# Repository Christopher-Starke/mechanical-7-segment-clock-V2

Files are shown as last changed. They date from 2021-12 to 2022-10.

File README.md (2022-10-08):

# mechanical-7-segment-clock-V2
A large mechanical 7-segment clock using cheap stepper motors. This thing is really big about 135x65cm! 

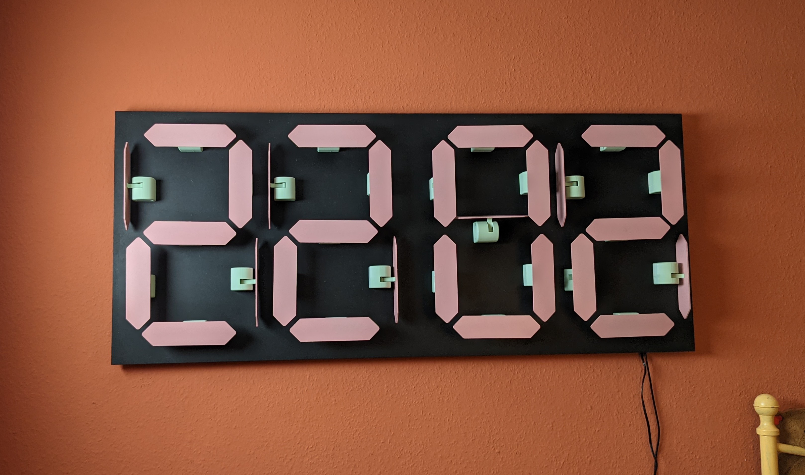
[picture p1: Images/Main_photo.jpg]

##

## BOM
- 28x		28BYJ-48 5V stepper motors (12v steppers also usable with appropriate power supply) 
- 1x		Main controller PCB
- 4x		Stepper breakout PCB
- 1x		button breakout PCB
- 28x		608 skateboard bearings
- 56x		M4x10 bolts (for anchoring stepper motors to the housing)
- 56x 		M4x25 bolts (for attaching the stepper casing to the backboard)
- 4x 		40 Pin ribbon cable connectors
- 1x		6 Pin ribbon cable connector 

### Printed parts 
- 28x 		Stepper housing-Case
- 28x		Stepper housing-Clip
- 28x		Stepper housing-Lever

- 1x		Button breakout - Base
- 1x		Button breakout - Lid

- 4x		Stepper breakout - base
- 4x 		Stepper breakout - lid 

- 1x		Controller - base
- 1x		Controller - lid 

### Cut parts
- 1x 		Backplate 	(18mm MDF)
- 28x		Segment 	(3mm MDF)

meep

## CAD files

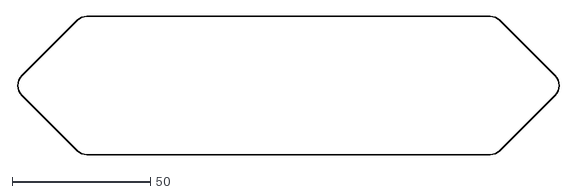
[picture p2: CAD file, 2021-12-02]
hardware/Cut files/Segment.dxf
196.8 x 50.0

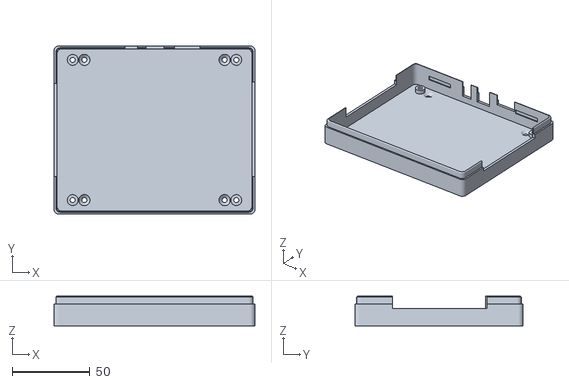
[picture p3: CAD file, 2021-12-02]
hardware/Print files/Electronics cases/Controller - base.stl
129.0 x 108.0 x 19.0

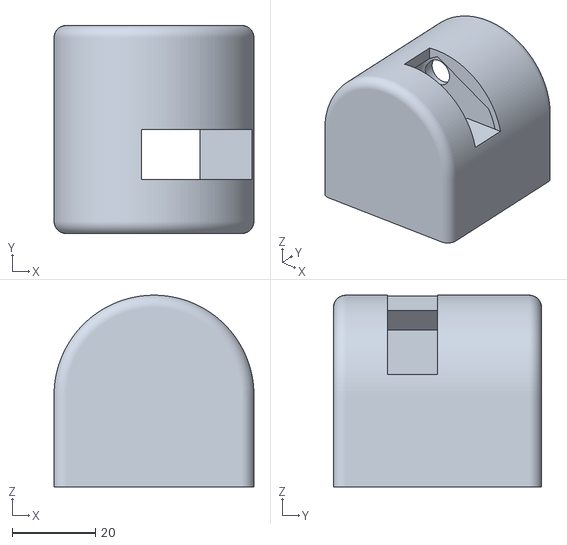
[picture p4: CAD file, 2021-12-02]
hardware/Print files/Stepper housing/Stepper housing - Case.stl
48.0 x 50.0 x 46.0

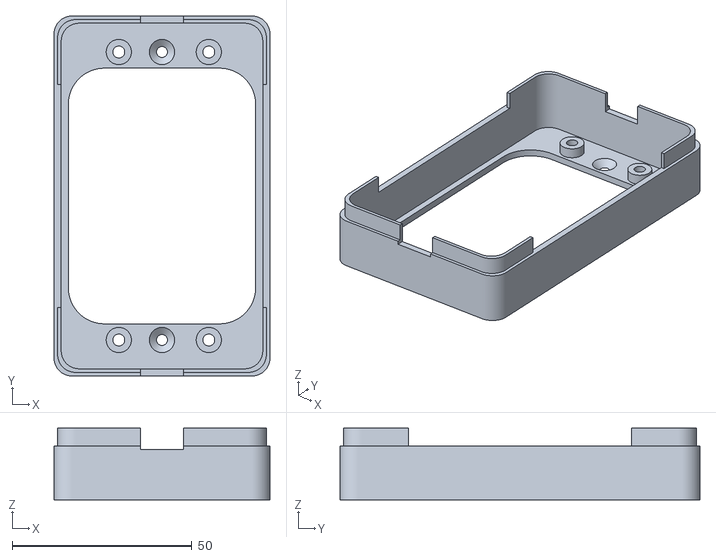
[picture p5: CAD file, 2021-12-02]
hardware/Print files/Electronics cases/Stepper breakout - base.stl
60.0 x 100.0 x 20.0

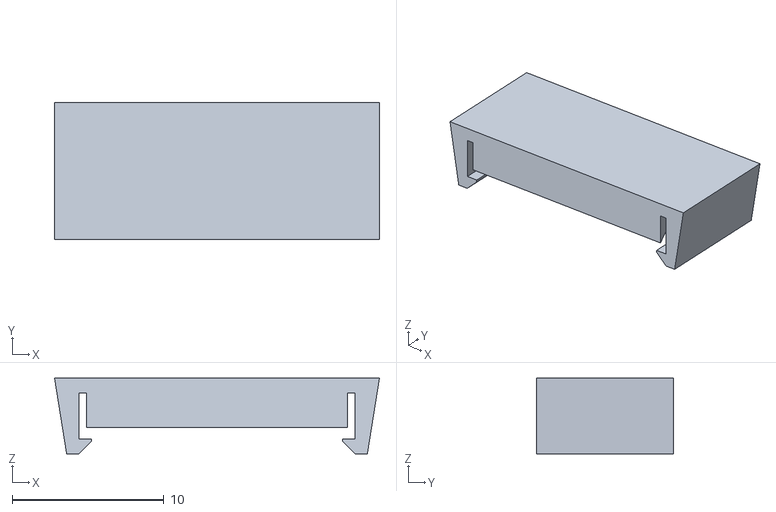
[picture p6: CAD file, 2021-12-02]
hardware/Print files/Stepper housing/Stepper housing - Clip.stl
21.4 x 9.00 x 5.00

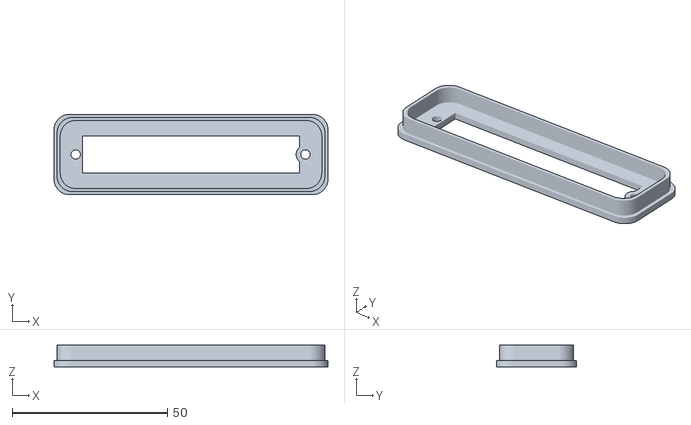
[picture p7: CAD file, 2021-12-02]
hardware/Print files/Electronics cases/Button breakout - Base.stl
88.3 x 25.9 x 7.00

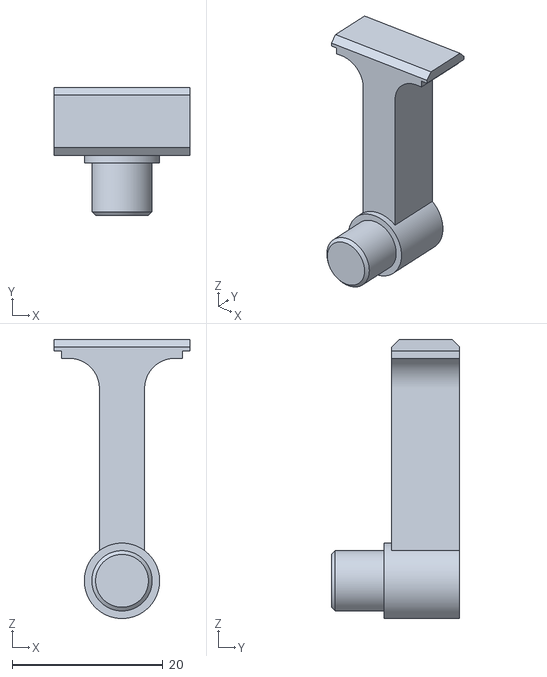
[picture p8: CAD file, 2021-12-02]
hardware/Print files/Stepper housing/Stepper housing - Lever.stl
18.0 x 17.0 x 37.0

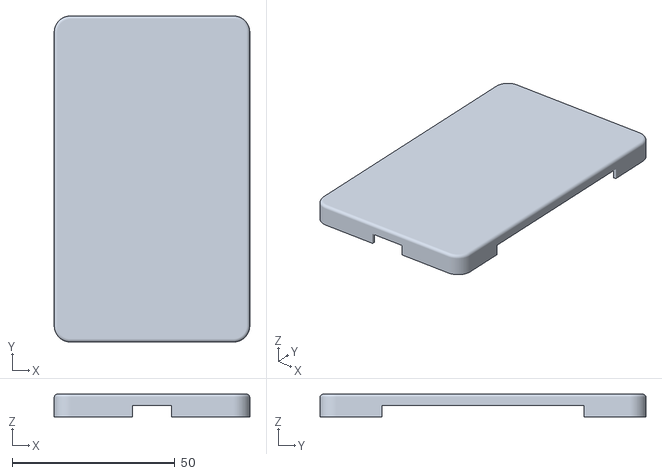
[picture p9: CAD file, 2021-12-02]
hardware/Print files/Electronics cases/Stepper breakout - lid.stl
60.0 x 100.0 x 7.00

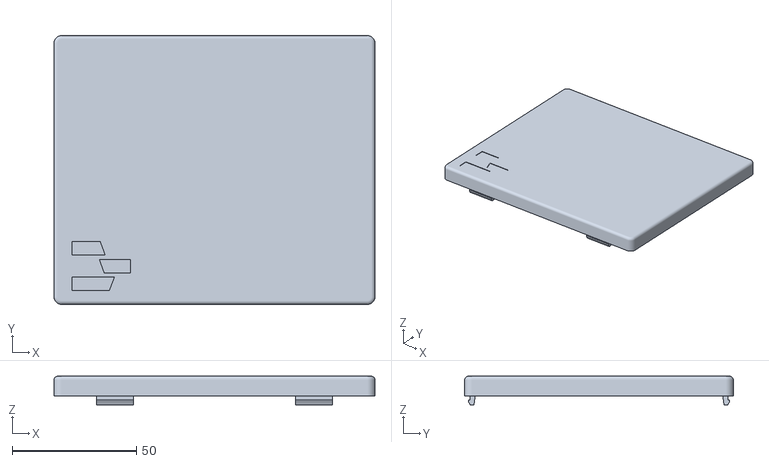
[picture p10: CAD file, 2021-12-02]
hardware/Print files/Electronics cases/Controller - lid.stl
129.0 x 108.0 x 11.5

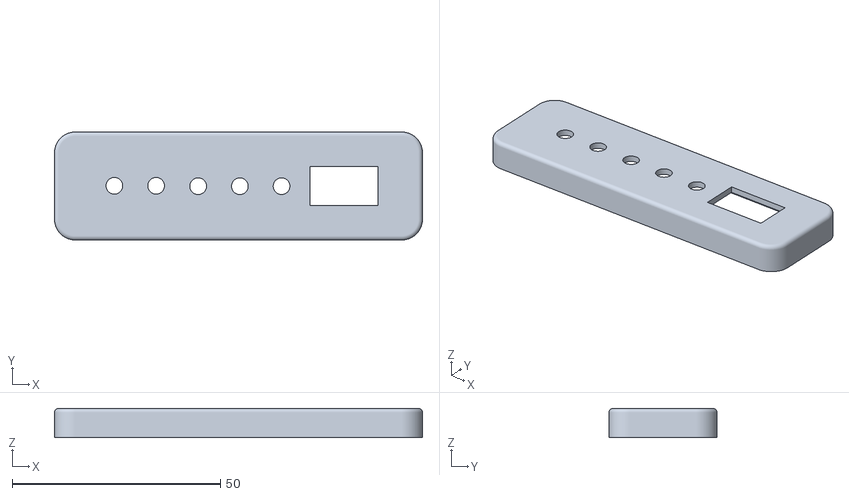
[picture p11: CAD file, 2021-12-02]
hardware/Print files/Electronics cases/Button breakout - Lid.stl
88.3 x 25.9 x 7.00

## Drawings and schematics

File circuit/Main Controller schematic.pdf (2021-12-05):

CN5 1

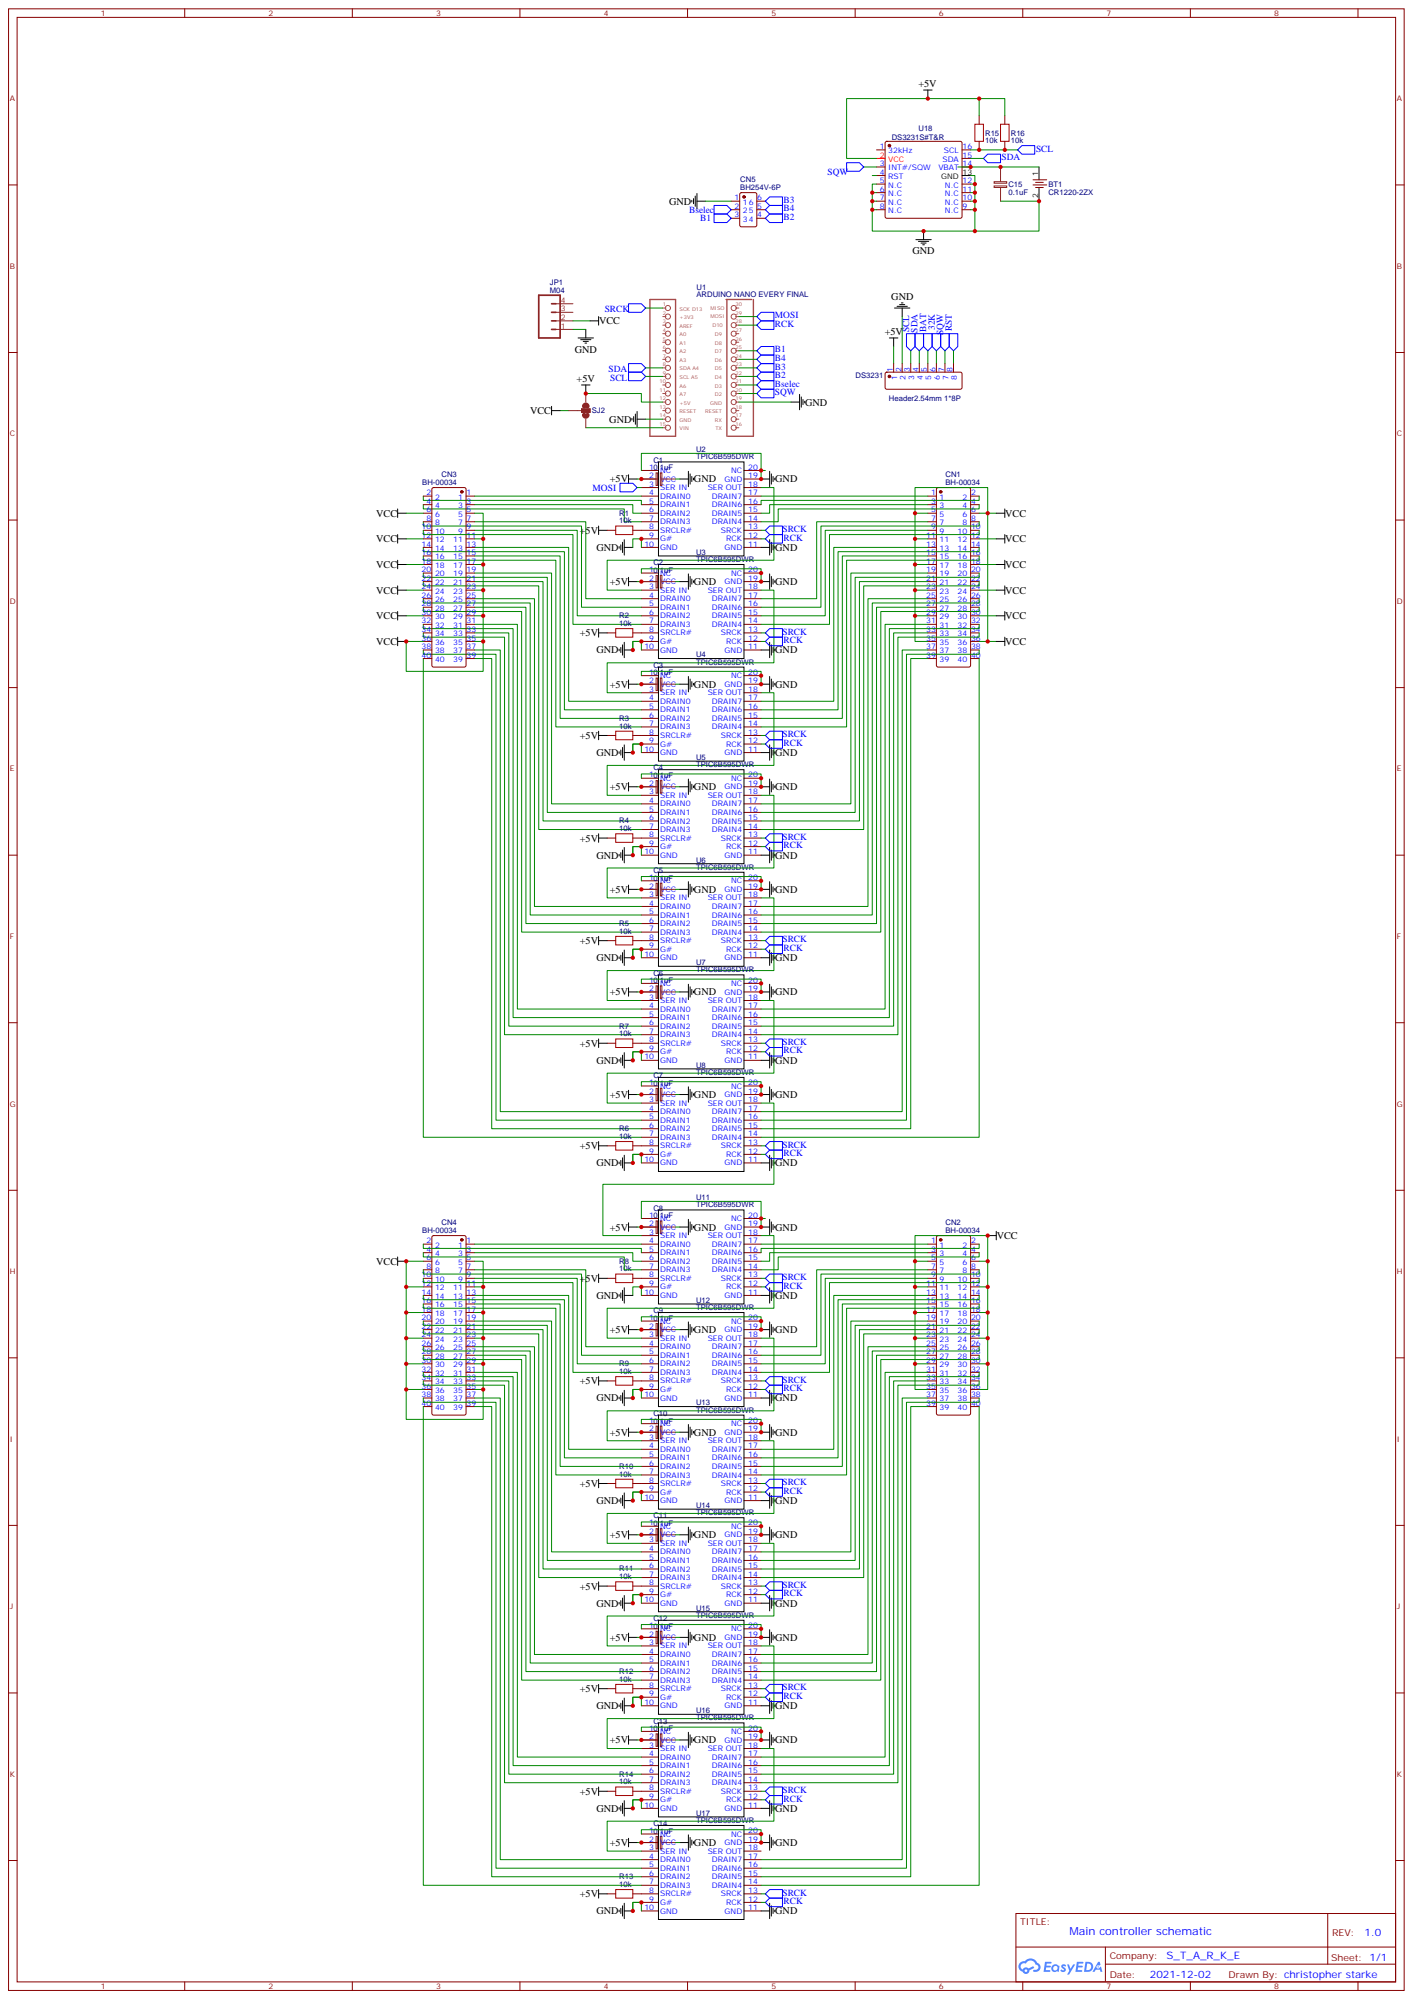
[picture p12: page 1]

ARDUINO NANO EVERY FINAL

Drawn By: christopher starke

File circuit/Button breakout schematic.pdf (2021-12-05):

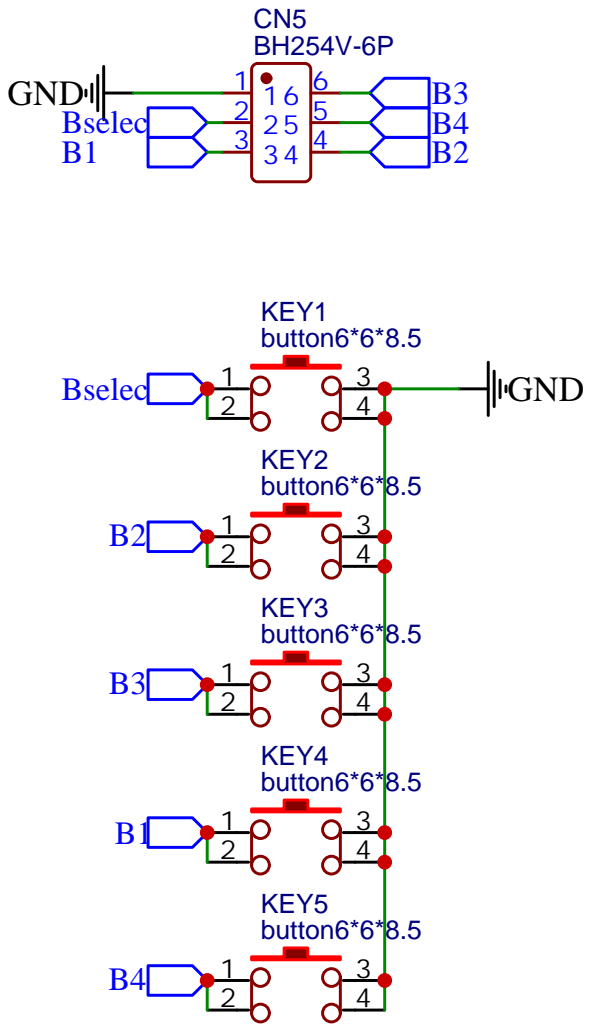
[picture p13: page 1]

Drawn By: christopher starke

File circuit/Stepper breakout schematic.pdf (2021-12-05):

J141

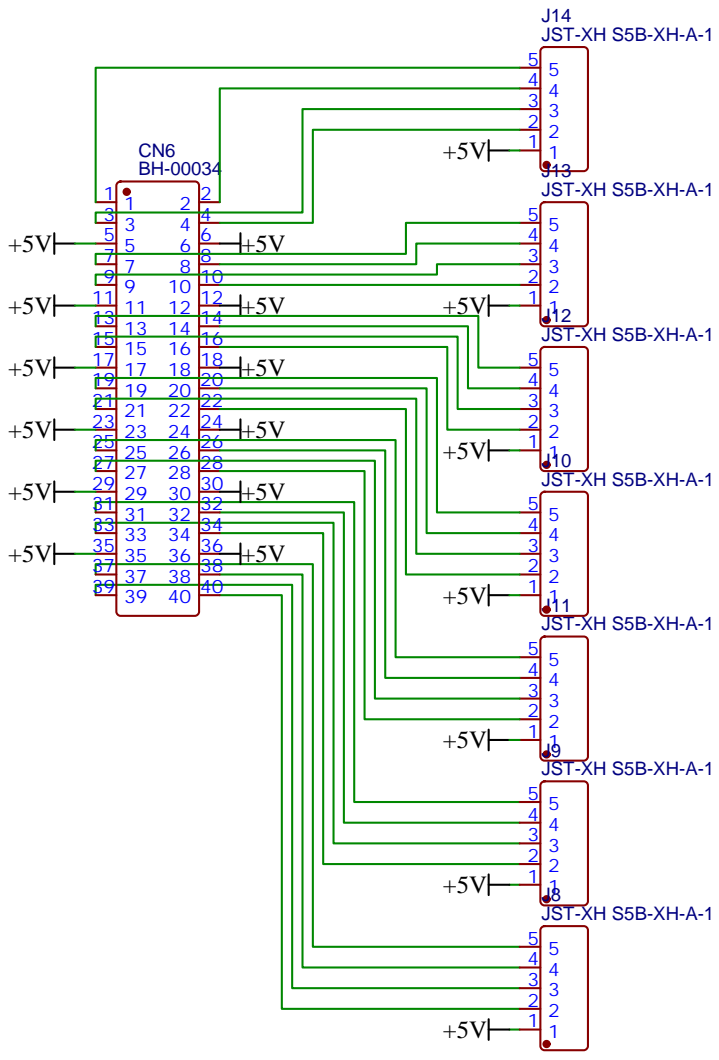
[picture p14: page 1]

Drawn By: christopher starke

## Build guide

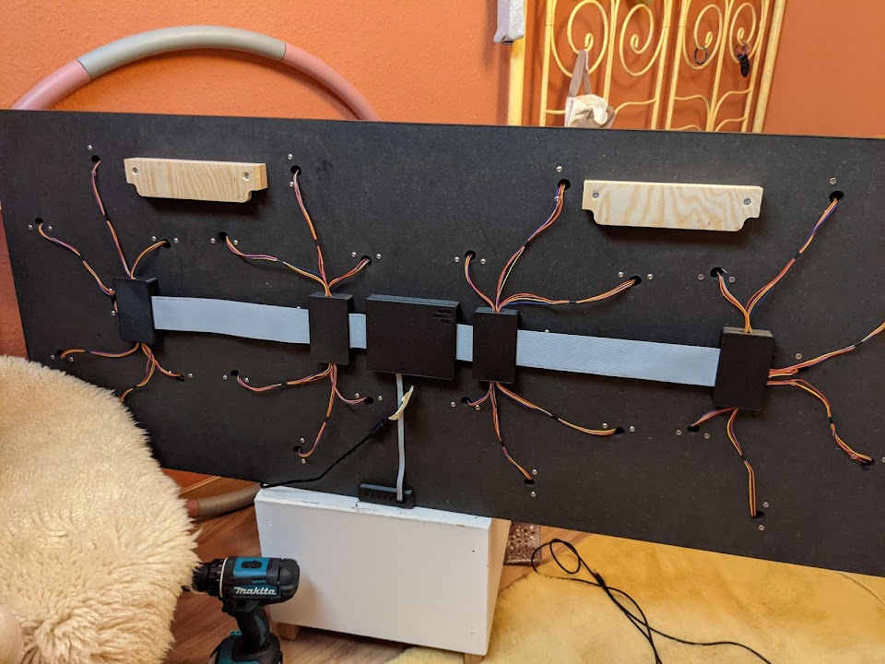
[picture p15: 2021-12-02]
Images/back_wiring.jpg

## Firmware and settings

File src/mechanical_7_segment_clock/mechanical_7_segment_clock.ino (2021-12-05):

#include "SPI.h"
#include "Wire.h"
#include "RTClib.h"
uint8_t segmentOrder[12] = {0b01111110, 0b00110000, 0b01101101, 0b01111001, 0b00110011, 0b01011011, 0b01011111, 0b01110000, 0b01111111, 0b01111011, 0b00000001, 0b00000000}; //
// ####### Segement order numbers #######
// _       _   _       _   _   _   _   _
//| |   |  _|  _| |_| |_  |_    | |_| |_|  _
//|_|   | |_   _|   |  _| |_|   | |_|  _|
// 0    1   2   3   4   5   6   7   8   9  10   11   // 11 is all segments in off position
const uint8_t stepOrder[9] = {0b00000000, 0b00000001, 0b00000011, 0b00000010, 0b00000110, 0b00000100, 0b00001100, 0b00001000, 0b00001001}; //binary order for stepper movement
const int8_t boardMap[28] = {2, 9, 3, 10, 4, 11, 0, 7, 5, 12, 6, 13, 1, 8, 26, 19, 27, 20, 22, 15, 21, 14, 23, 16, 24, 17, 25, 18};        //mapping of the board pin output to segments
const int8_t direction[4] = {1, -1, -1, 1};                                                                                                // Direction to move to open all segments
int8_t currentStep[28] = {1, 1, 1, 1, 1, 1, 1, 1, 1, 1, 1, 1, 1, 1, 1, 1, 1, 1, 1, 1, 1, 1, 1, 1, 1, 1, 1, 1};
uint32_t stepsPerMove = 1200; //1200;  /// set correctly 4096/rev
uint32_t stepRate = 900;      //delay between steps in micro seconds min 800
uint32_t mask;
uint8_t byteOut = 0b00000000;
uint8_t nibbleOutCount = 0;
const int slaveSelectPin = 10;
uint32_t timer;
const char compile_date[] = __DATE__ " " __TIME__;
byte Minutes = 0;
byte Hour = 0;
uint8_t timeArray[4] = {11, 11, 11, 11}; //{min digit, min tens,hour digit, hour tens} // 11 is a fully open digit IE all segments folded back
uint8_t oldTimeArray[4] = {8, 8, 8, 8};  //{min digit, min tens,hour digit, hour tens}
bool offOn = true;
unsigned long sleepTimerNew = 0;
unsigned long sleepTimerOld = 0;

RTC_DS3231 rtc;
#define CLOCK_INTERRUPT_PIN 2

uint8_t buttonPin[4] = {6, 7, 5, 4}; //
uint8_t ButtonState[4] = {LOW, LOW, LOW, LOW};
uint8_t lastButtonState[4] = {LOW, LOW, LOW, LOW}; //holds the previous button state
unsigned long lastDebounceTime[4] = {0, 0, 0, 0};
unsigned long debounceDelay = 50;

unsigned long watchdogTime = 61200; // one minute and 2 seconds
unsigned long watchdogTimer = 0;    // used to keep track of the millis() since the last rtc alarm

//*************************************************************************************************************************
//************************** Setup ****************************************************************************************
//*************************************************************************************************************************

void setup()
{
  pinMode(slaveSelectPin, OUTPUT);
  SPI.beginTransaction(SPISettings(500000, LSBFIRST, SPI_MODE0));
  SPI.begin();
  Serial.begin(9600);
  directMove(); //Set the segment to open position
  Serial.println("poop");

  for (int i = 0; i < 4; i++)
  {
    pinMode(buttonPin[i], INPUT_PULLUP);
  }

  int8_t x = 0;
  while (x <= 1) // used to test the display on startup
  {
    timeArray[0] = x;
    timeArray[1] = x;
    timeArray[2] = x;
    timeArray[3] = x;
    directMove();
    delay(100);
    x++;
  }

  if (!rtc.begin())
  {
    Serial.println("Couldn't find RTC");
    Serial.flush();
    abort();
  }
  if (rtc.lostPower())
  {
    rtc.adjust(DateTime(F(__DATE__), F(__TIME__)));
  }
  rtc.disable32K();                           //we don't need the 32K Pin, so disable it
  pinMode(CLOCK_INTERRUPT_PIN, INPUT_PULLUP); // Making it so, that the alarm will trigger an interrupt
  attachInterrupt(digitalPinToInterrupt(CLOCK_INTERRUPT_PIN), onAlarm, FALLING);
  rtc.clearAlarm(1); // set alarm 1, 2 flag to false (so alarm 1, 2 didn't happen so far)
  rtc.clearAlarm(2);
  rtc.writeSqwPinMode(DS3231_OFF);                              // stop oscillating signals at SQW Pin
  rtc.disableAlarm(2);                                          // turn off alarm 2 (in case it isn't off already)
  rtc.setAlarm1(DateTime(0, 0, 0, 0, 0, 00), DS3231_A1_Second); // schedule an alarm at the next minute seconds in the future
}

//*************************************************************************************************************************
//************************** Loop *****************************************************************************************
//*************************************************************************************************************************

void loop()
{

  if (rtc.alarmFired(1) || (millis() - watchdogTimer > watchdogTime))
  {                           // if the rtc alarm flag is high update the time second function is there to identify if the rtcalarm function failed
    watchdogTimer = millis(); // reset the watchdog timer
    DateTime now = rtc.now();
    rtc.clearAlarm(1);                                            // clear the alarm flag
    rtc.setAlarm1(DateTime(0, 0, 0, 0, 0, 00), DS3231_A1_Second); // reset the alarm to trigger the next minute

    Minutes = now.minute(); // Break up the time into its digits
    timeArray[1] = Minutes / 10;
    timeArray[0] = Minutes - timeArray[1] * 10;

    Hour = now.hour();
    timeArray[3] = Hour / 10;
    timeArray[2] = Hour - timeArray[3] * 10;

    if (Hour < 21 && Hour > 7)
    { // used to disable the clock at night
      offOn = true;
      directMove();
    }
    else if (offOn)
    {
      timeArray[0] = 10;
      timeArray[1] = 10;
      timeArray[2] = 10;
      timeArray[3] = 10;
      offOn = false;
    }
  }
  sleepPower(); // reduces the power consumption of the clock between minute changes
  buttonPolling();
}

//*************************************************************************************************************************
//************************** Button polling  ******************************************************************************
//*************************************************************************************************************************

void buttonPolling()
{

  for (int i = 0; i < 4; i++)
  {
    //rtc.adjust( rtc.now() + getdatetime.timedelta(minutes = 10)); // move minutes up by ten
    int reading = digitalRead(buttonPin[i]);
    if (reading != lastButtonState[i])
    {
      // reset the debouncing timer
      lastDebounceTime[i] = millis();
    }

    if (millis() - lastDebounceTime[i] > debounceDelay)
    {
      if (reading != ButtonState[i])
      {
        ButtonState[i] = reading;

        if (lastButtonState[i] == LOW)
        {
          DateTime now = rtc.now();
          Minutes = now.minute(); // Break up the time into its digits
          timeArray[1] = Minutes / 10;
          timeArray[0] = Minutes - timeArray[1] * 10;
          Hour = now.hour();
          timeArray[3] = Hour / 10;
          timeArray[2] = Hour - timeArray[3] * 10;
          int Seconds = now.minute();
          

          switch (i)
          {
          case 0:
            timeArray[0]++;
            if (timeArray[0] > 9)
            { // rollover
              timeArray[0] = 0;
            }
            Seconds = 01; //set the seconds to 1 to make the minute start when pressed
            break;
          case 1:
            timeArray[1]++;
            if (timeArray[1] > 5)
            { // rollover
              timeArray[1] = 0;
            }
            break;
          case 2:
            timeArray[2]++;
            if (timeArray[2] > 9)
            { // rollover
              timeArray[2] = 0;
            }
            break;
          case 3:
            timeArray[3]++;
            if (timeArray[3] > 2)
            { // rollover
              timeArray[3] = 0;
            }
            break;
          }

          Minutes = timeArray[1] * 10 + timeArray[0];
          Hour = timeArray[3] * 10 + timeArray[2];
          DateTime newTime = {now.year(), now.month(), now.day(), Hour, Minutes, Seconds};
          rtc.adjust(newTime);
          directMove();
          //Serial.println("pooop");

          /*char date[10] = "hh:mm:ss";
          newTime.toString(date);
          Serial.println(date);
        */
        }
      }
    }
    lastButtonState[i] = reading;
  }
}

//*************************************************************************************************************************
//************************** Sleep Power Function *************************************************************************
//*************************************************************************************************************************

void sleepPower()
{

  digitalWrite(slaveSelectPin, HIGH);
  int segmentPush = 0;
  sleepTimerNew = micros();
  while (segmentPush < 28)
  { // send out next step over spi
    if ((sleepTimerNew - sleepTimerOld) < 100)
    {
      byteOut = byteOut | stepOrder[currentStep[boardMap[segmentPush]]] << 4 * nibbleOutCount;
    }
    else if ((sleepTimerNew - sleepTimerOld) < 50)
    {
      byteOut = 0b00000000;
    }
    nibbleOutCount++;

    if (nibbleOutCount == 2)
    { // collate steps into SPI byte
      SPI.transfer(byteOut);
      byteOut = 0b00000000;
      nibbleOutCount = 0;
    }
    segmentPush++;
  }
  if ((sleepTimerNew - sleepTimerOld) >= 700)
  {
    sleepTimerOld = sleepTimerNew;
  }
  digitalWrite(slaveSelectPin, LOW);
}
//*************************************************************************************************************************
//************************** Direct Move Function *************************************************************************
//*************************************************************************************************************************
void directMove()
{

  int stepsToGo = stepsPerMove;

  while (stepsToGo > 0)
  {
    int digit = 0;
    while (digit < 4)
    {
      uint8_t oldSegments = segmentOrder[oldTimeArray[digit]];
      uint8_t newSegments = segmentOrder[timeArray[digit]];
      //Serial.print(digit,DEC);
      int segment = 0;
      while (segment < 7)
      {
        int adjustedSegment = segment + digit * 7;
        if (bitRead(oldSegments, segment) == 1)
        {
          currentStep[adjustedSegment] = currentStep[adjustedSegment] + direction[digit]; //increment in desired direction
          if (currentStep[adjustedSegment] == 9)
          {
            currentStep[adjustedSegment] = 1; //rollover
          }
          if (currentStep[adjustedSegment] == 0)
          {
            currentStep[adjustedSegment] = 8; //rollover
          }
        }
        if (bitRead(newSegments, segment) == 1)
        {
          currentStep[adjustedSegment] = currentStep[adjustedSegment] - direction[digit]; //increment in desired direction
          if (currentStep[adjustedSegment] == 9)
          {
            currentStep[adjustedSegment] = 1; //rollover
          }
          if (currentStep[adjustedSegment] == 0)
          {
            currentStep[adjustedSegment] = 8; //rollover
          }
        }
        segment++;
      }
      digit++;
    }

    digitalWrite(slaveSelectPin, HIGH);
    int segmentPush = 0;

    while (segmentPush < 28)
    { // send out next step over spi

      byteOut = byteOut | stepOrder[currentStep[boardMap[segmentPush]]] << 4 * nibbleOutCount;
      nibbleOutCount++;

      if (nibbleOutCount == 2)
      { // collate steps into SPI byte
        SPI.transfer(byteOut);
        byteOut = 0b00000000;
        nibbleOutCount = 0;
      }
      segmentPush++;
    }

    digitalWrite(slaveSelectPin, LOW);
    stepsToGo = stepsToGo - 1;
    while (micros() - timer < stepRate)
    {
      ;
    }
    timer = micros();
    digit++;
  }

  oldTimeArray[0] = timeArray[0];
  oldTimeArray[1] = timeArray[1];
  oldTimeArray[2] = timeArray[2];
  oldTimeArray[3] = timeArray[3];
}

//*************************************************************************************************************************
//************************** Alarm ISR ************************************************************************************
//*************************************************************************************************************************
void onAlarm()
{ //minuteAlarm
}
